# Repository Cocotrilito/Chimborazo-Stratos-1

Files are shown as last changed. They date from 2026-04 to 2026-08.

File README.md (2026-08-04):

# Chimborazo-Stratos-1 V2
"Designed at the world's closest point to the stars." - me =p A custom Model Rocket Flight Computer (CFC) designed for high-altitude stabilization and recovery. It features an IMU for orientation tracking and a barometer for apogee detection. The goal is to create a reliable, low-cost brain for amateur rocketry in Ecuador.
## The reason behind this project
**"When something is important enough, you do it even if the odds are not in your favor."** *— Elon Musk*
This project is born with the intent of giving my homecountry a posibility or even a first step to develop new technology, maybe *inspire* others just like Astrounauts or cientifics inspired me.
## It's Alive!

<p align="center">
  Chimborazo Stratos-1 running
</p>

<p align="center">
  
</p>

First bring-up worked. The IMU and the barometer both came up on I2C at `0x68` and `0x77`, and the board is now streaming live telemetry over serial at 115200 baud.

Ground pressure read **75207 Pa**. Sea level is 101325 Pa, so the board is literally measuring the real atmosphere of Quito at ~2800m. Altitude noise is around ±0.1m, which is good enough for apogee detection.

The flight state machine goes `ARMED → BOOST → COAST → APOGEE → DESCENT`. Liftoff fires on an acceleration spike above 25 m/s², apogee on a 2m drop from peak altitude. Sensors are read at 50Hz and the dashboard prints every 3 seconds.
## Schematic Overview

<p align="center">
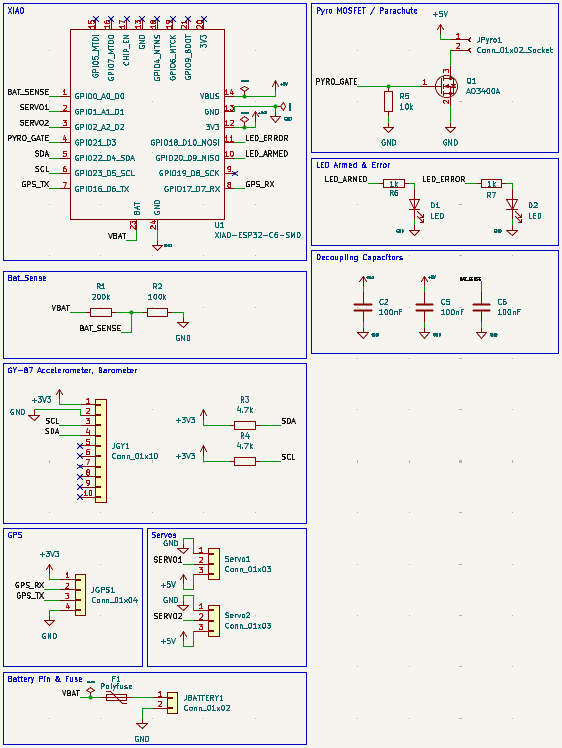
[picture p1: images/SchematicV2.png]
Chimborazo Stratos-1 Schematic model in KiCad
  
</p>

## PCB

<p align="center">
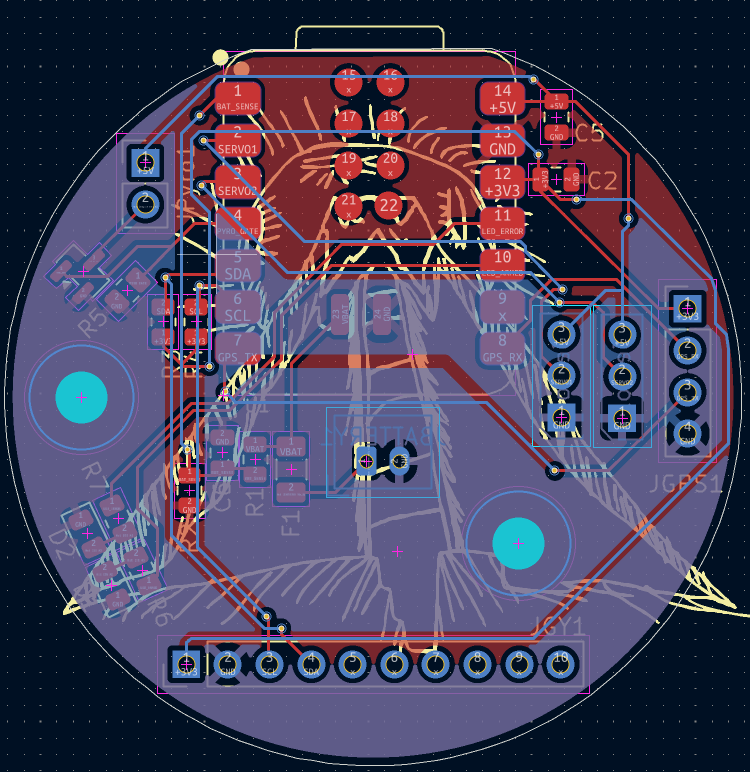
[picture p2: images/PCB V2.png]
PCB layout
  
</p>

<table>
  <tr>
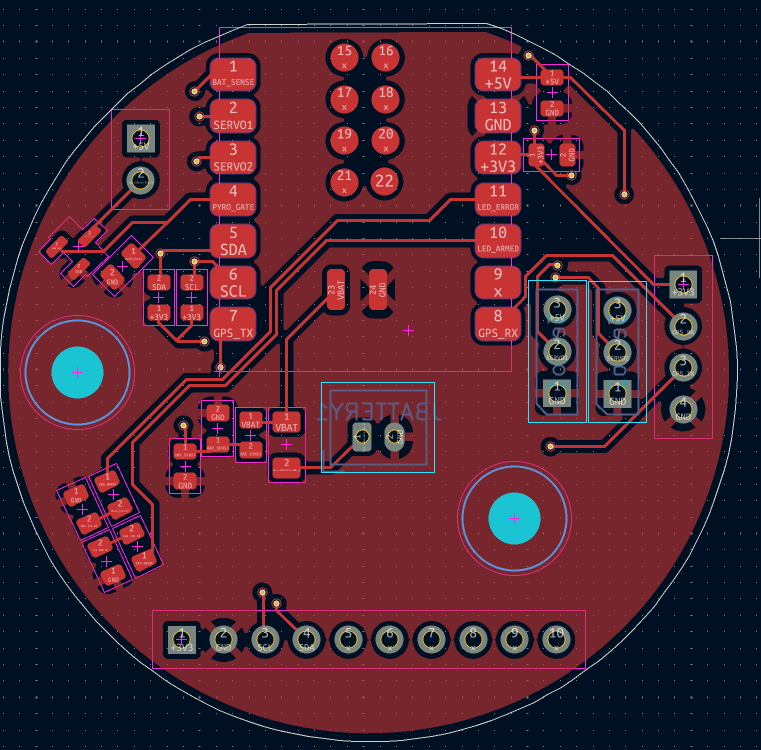
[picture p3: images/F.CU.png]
Front copper
    <td width="50%"></td>
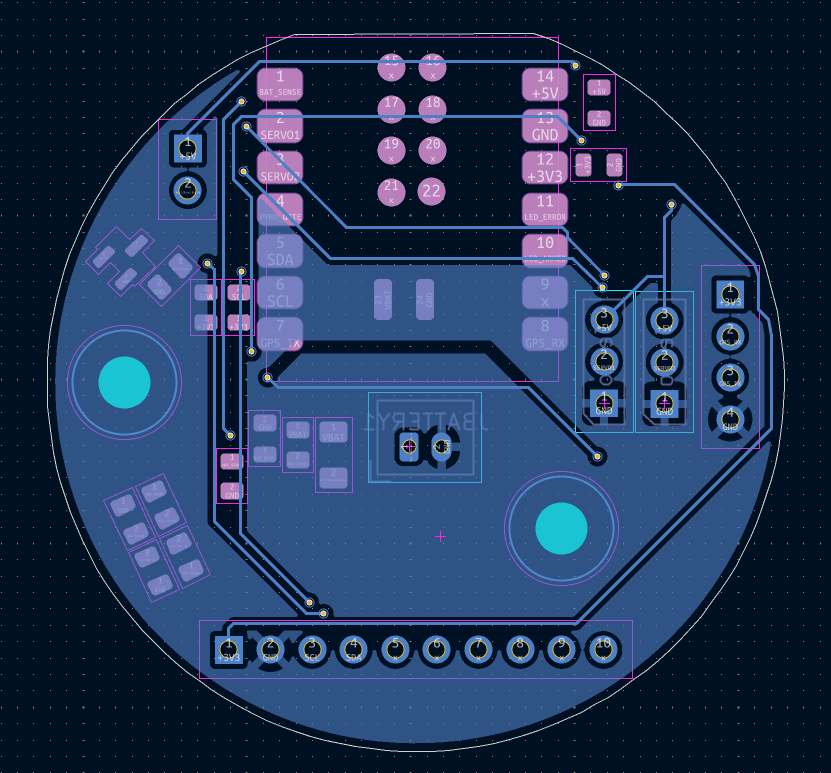
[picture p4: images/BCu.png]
Back copper
    <td width="50%"></td>
  </tr>
  <tr>
    <td align="center"><b>Front Copper</b></td>
    <td align="center"><b>Back Copper</b></td>
  </tr>
</table>

## CAD MODEL

<p align="center">
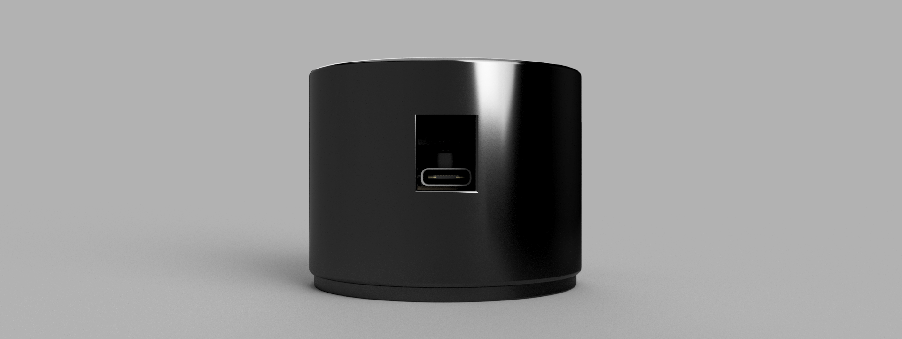
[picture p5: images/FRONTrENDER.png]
Final render
  
</p>

<table>
  <tr>
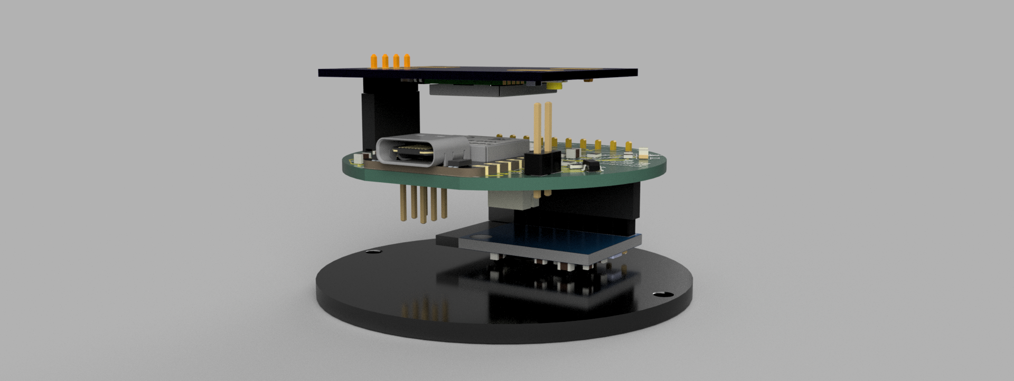
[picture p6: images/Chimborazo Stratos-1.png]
Side view
    <td width="50%"></td>
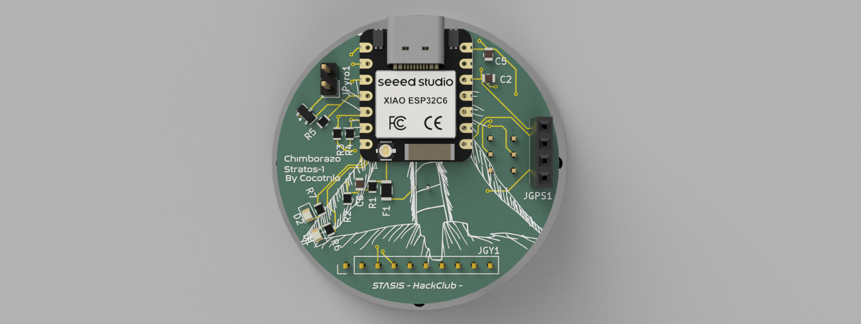
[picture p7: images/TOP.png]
Top view
    <td width="50%"></td>
  </tr>
  <tr>
    <td align="center"><b>Side View</b></td>
    <td align="center"><b>Top View</b></td>
  </tr>
</table>

## Bom 
| Name | Purpose | Qty | Total Cost (USD) | Link |
| :--- | :--- | :---: | :---: | :--- |
| **XIAO ESP32-C6** | Main Flight Computer / MCU | 1 | $11.08 | [AliExpress](https://www.aliexpress.com/item/3256808627180483.html) |
| **GY-87 10DOF** | IMU & Barometer (Orientation/Altitude) | 1 | $1.53 | [AliExpress](https://www.aliexpress.com/item/3256807064707842.html) |
| **ATGM336H GPS** | Global Positioning System Module | 1 | $1.93 | [AliExpress](https://www.aliexpress.com/item/3256810342214632.html) |
| **SG90 Servos (2pcs)** | Canard Actuators (Active Stabilization) | 1 | $1.33 | [AliExpress](https://www.aliexpress.com/item/3256807031850814.html) |
| **JST PH 2.0 Connectors** | LiPo Battery Connection Set | 1 | $1.53 | [AliExpress](https://www.aliexpress.com/item/3256808243626691.html) |
| **40-Pin Headers (M/F)** | Interconnection & Sensor Mounting | 1 | $0.93 | [AliExpress](https://www.aliexpress.com/item/3256811594914967.html) |
| **JLCPCB PCBA** | PCB Manufacturing + SMT Assembly | 1 | $22.46 | [JLCPCB](https://jlcpcb.com) |
## Things I learned the hard way
- The GY-87 has 8 pins starting with `VCC_IN` but my PCB only breaks out 4. Turns out you can feed 3.3V straight into the `3V3` pin and skip the module's onboard regulator entirely. Left `VCC_IN` hanging off the edge and it worked.
- The SG90 servos were browning out my USB port on startup and killing my uploads. In flight they go on the LiPo, never on USB.
- This GY-87 ships with a **BMP180**, not a BMP280. Needs the `Adafruit_BMP085` library.
- The HMC5883L magnetometer hides behind the MPU6050's auxiliary bus. It only shows up at `0x1E` after enabling bypass mode with `INT_PIN_CFG = 0x02`.
## What's next
- [ ] Solder the JST PH 2.0 for the LiPo
- [ ] GPS satellite lock (UART is open, needs open sky)
- [ ] Servo control and canard stabilization
- [ ] Onboard flight data logging
## Final Notes
Thanks for reading! made possible with http://stasis.hackclub.com/
New version! after review
## Dreams
*By cocotrilo*
**made with luv <3**

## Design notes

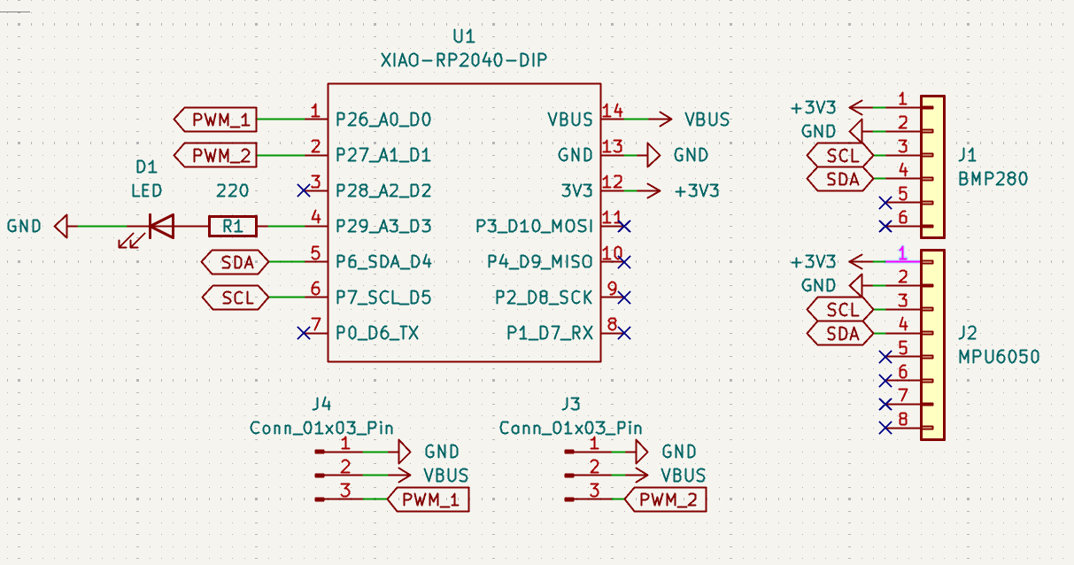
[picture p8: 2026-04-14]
images/Schematic.png

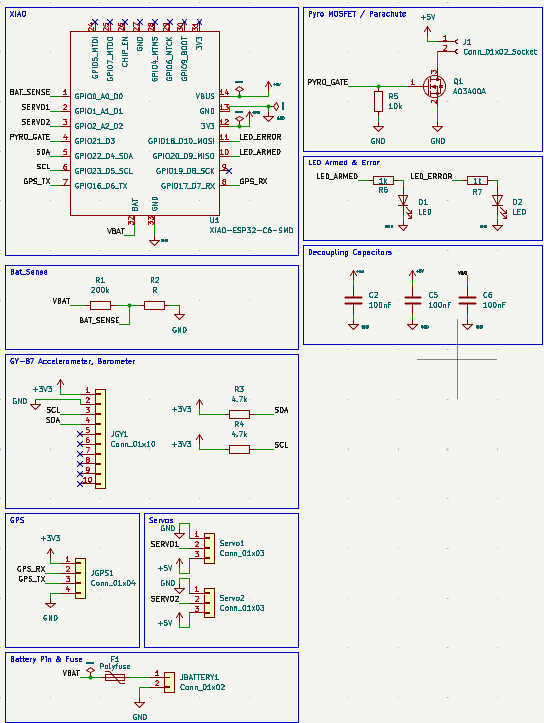
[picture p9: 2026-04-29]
images/SchematicUPDATE.png

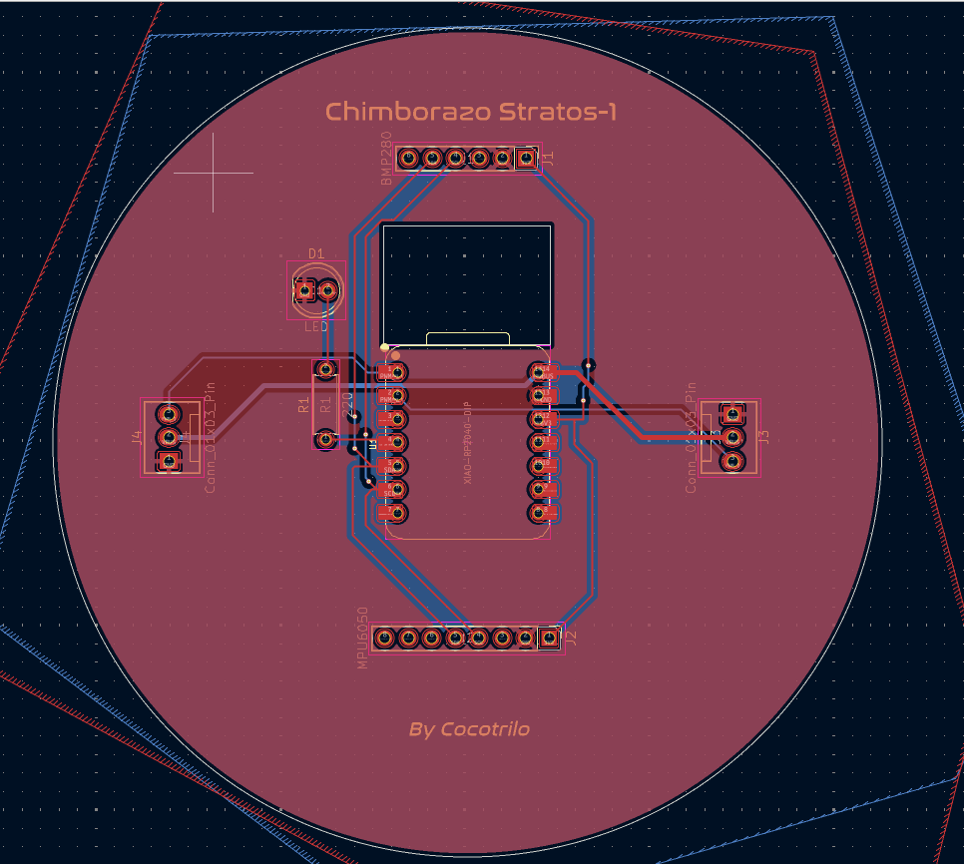
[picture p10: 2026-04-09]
images/08-04-26 PCB.png

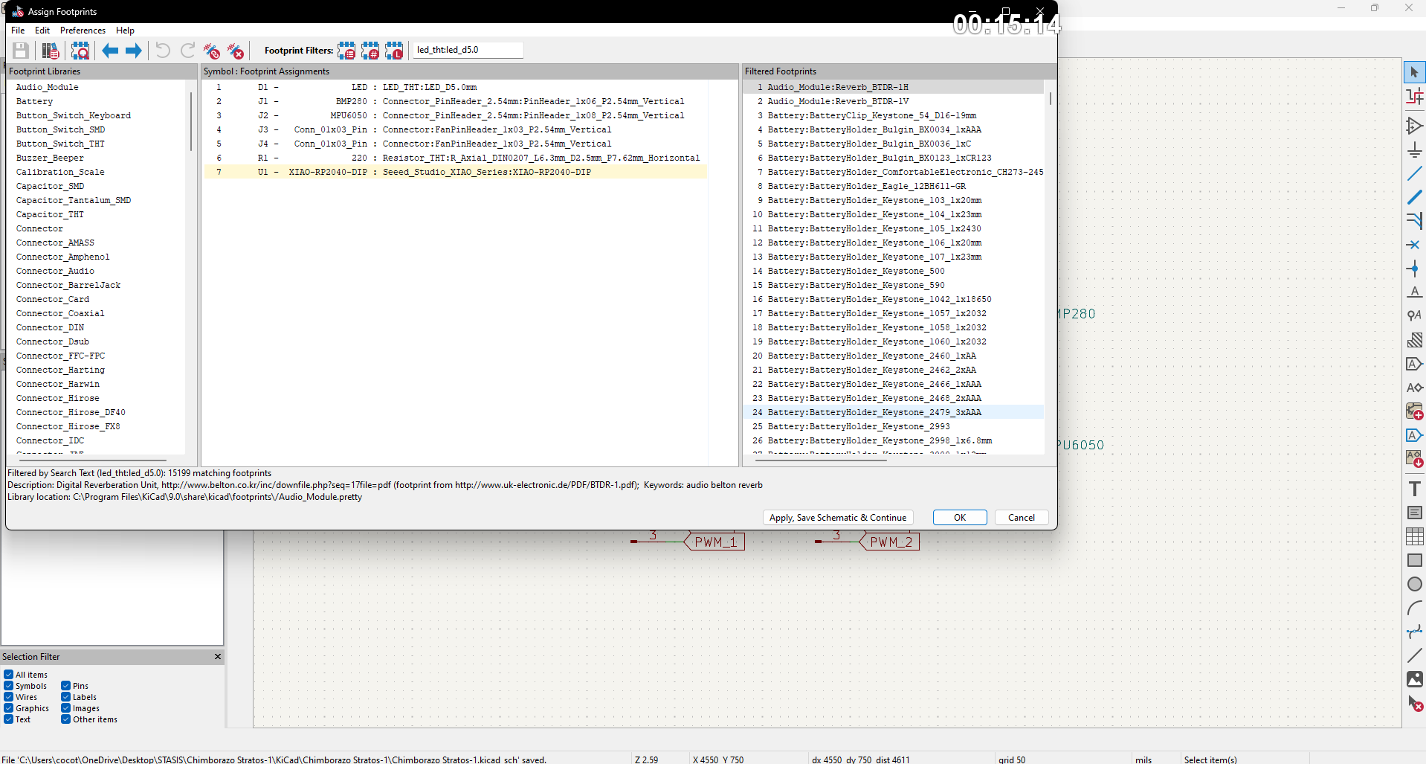
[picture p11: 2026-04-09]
images/08-04-26 FOOTPRITNS.png

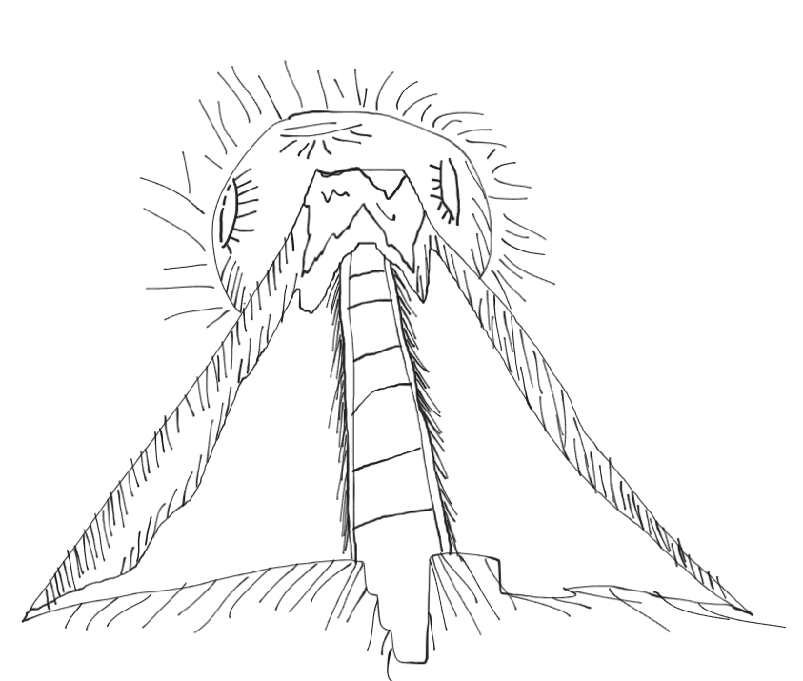
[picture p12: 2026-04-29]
images/art.png

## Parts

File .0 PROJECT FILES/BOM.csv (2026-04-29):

Name | Purpose | Qty | Total Cost (USD) | Link
XIAO ESP32-C6 | Main Flight Computer / MCU | 1 | 11.08 | https://www.aliexpress.com/item/3256808627180483.html
GY-87 10DOF | IMU & Barometer (Orientation/Altitude) | 1 | 1.53 | https://www.aliexpress.com/item/3256807064707842.html
ATGM336H GPS | Global Positioning System Module | 1 | 1.93 | https://www.aliexpress.com/item/3256810342214632.html
SG90 Servos (2pcs) | Canard Actuators (Active Stabilization) | 1 | 1.33 | https://www.aliexpress.com/item/3256807031850814.html
JST PH 2.0 Connectors | LiPo Battery Connection Set | 1 | 1.53 | https://www.aliexpress.com/item/3256808243626691.html
40-Pin Headers (M/F) | Interconnection & Sensor Mounting | 1 | 0.93 | https://www.aliexpress.com/item/3256811594914967.html
JLCPCB PCBA | PCB Manufacturing + SMT Assembly | 1 | 22.46 | https://jlcpcb.com
Taxes & Customs | Estimated Import Duties | 1 | 5 | -

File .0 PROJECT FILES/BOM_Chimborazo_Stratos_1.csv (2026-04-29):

Item | Descripcion | Proveedor | Cantidad | Precio_USD | Enlace | Subtotal
XIAO ESP32-C6 | Microcontrolador Principal | AliExpress | 1 | 11.08 | https://www.aliexpress.com/item/3256808627180483.html | 11.08
GY-87 10DOF | Sensor IMU + Barómetro | AliExpress | 1 | 1.53 | https://www.aliexpress.com/item/3256807064707842.html | 1.53
GPS ATGM336H | Posicionamiento Global | AliExpress | 1 | 1.93 | https://www.aliexpress.com/item/3256810342214632.html | 1.93
Servos SG90 (2pcs) | Actuadores Canards | AliExpress | 1 | 1.33 | https://www.aliexpress.com/item/3256807031850814.html | 1.33
JST PH 2.0 Connector | Conector Batería | AliExpress | 1 | 1.53 | https://www.aliexpress.com/item/3256808243626691.html | 1.53
40 Pin Headers (M/F) | Conectores | AliExpress | 1 | 0.93 | https://www.aliexpress.com/item/3256811594914967.html | 0.93
JLCPCB PCBA | PCB + Montaje SMD | JLCPCB | 1 | 22.46 | https://jlcpcb.com | 22.46
Tax / Impuestos | Aranceles estimados | Aduana | 1 | 5.0 | - | 5.0

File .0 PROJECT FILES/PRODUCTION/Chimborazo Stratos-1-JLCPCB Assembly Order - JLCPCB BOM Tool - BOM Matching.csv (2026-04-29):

JLCPCB BOM Tool - BOM Matching
BOM name：Chimborazo Stratos-1-JLCPCB Assembly Order.xlsx |  |  | Download Time：2026-04-30 01:16:50 |  |  |  | * Our matching results are updated in real-time, but stock and prices may change. If it's been over 24 hours, please re-match before placing your order.
PCB Assembled Qty：5 |  |  | Est. Total Price：0.4023
Your BOM |  |  |  |  | Matched Parts |  |  |  |  |  |  | Order Information
Top Designator | Bottom Designator | Comment | Footprint | JLCPCB Part # | Matches | Part # | Manufacturer | Footprint | Description | Category | Warning | JLCPCB Part # | Product link | Lib Type | Qty | Source | Total Price ($)
C2,C5,C6 |  | 100nF | C_0805_2012Metric |  | Select by Customer | CC0805KRX7R9BB104 | YAGEO | 0805 | 100nF 50V X7R ±10% 0805 Multilayer Ceramic Capacitors MLCC - SMD/SMT ROHS | Multilayer Ceramic Capacitors MLCC - SMD/SMT |  | C49678 | https://jlcpcb.com/partdetail/YAGEO-CC0805KRX7R9BB104/C49678 | Basic | 6 | 6 JLCPCB | 0.0312
D1,D2 |  | LED | LED_0805_2012Metric |  | Select by Customer | KT-0805Y | Hubei KENTO Elec | 0805 | -40℃~+85℃ 1.8V~2.4V 120° 175mcd 40mW 584nm~594nm 596nm Discrete Diode Water Clear Yellow 0805 LED Indication - Discrete ROHS | LED Indication - Discrete | 1.The comment (KT-0805Y) of this part does not match the one (LED) provided in your BOM. Please confirm; | C2296 | https://jlcpcb.com/partdetail/Hubei_KENTOElec-KT0805Y/C2296 | Basic | 4 | 4 JLCPCB | 0.06
F1 |  | Polyfuse | Fuse_1206_3216Metric |  | Select by Customer | 1206W4F6800T5E | UNI-ROYAL(Uniroyal Elec) | 1206 | -55℃~+155℃ 200V 250mW 680Ω Thick Film Resistor ±1% ±100ppm/℃ 1206 Chip Resistor - Surface Mount ROHS | Chip Resistor - Surface Mount |  | C17975 | https://jlcpcb.com/partdetail/18663-1206W4F6800T5E/C17975 | Extended | 15 | 15 JLCPCB | 0.0555
Q1 |  | AO3400A | SOT-23 |  | Select by Customer | AO3400A | Alpha & Omega Semicon | SOT-23 | -55℃~+150℃ 1 N-channel 1.45V 1.4W 30V 48mΩ@2.5V 5.7A 50pF 630pF 75pF 7nC@10V N-Channel SOT-23 MOSFETs ROHS | MOSFETs |  | C20917 | https://jlcpcb.com/partdetail/Alpha_OmegaSemicon-AO3400A/C20917 | Basic | 2 | 2 JLCPCB | 0.1634
R1 |  | 200k | R_0805_2012Metric |  | Select by Customer | 0805W8F2003T5E | UNI-ROYAL(Uniroyal Elec) | 0805 | -55℃~+155℃ 125mW 150V 200kΩ Thick Film Resistor ±1% ±100ppm/℃ 0805 Chip Resistor - Surface Mount ROHS | Chip Resistor - Surface Mount | 1.The comment (0805W8F2003T5E) of this part does not match the one (200k) provided in your BOM. Please confirm; | C17539 | https://jlcpcb.com/partdetail/18227-0805W8F2003T5E/C17539 | Basic | 2 | 2 JLCPCB | 0.0056
R2 |  | 100k | R_0805_2012Metric |  | Select by Customer | RC0805FR-07100KL | YAGEO | 0805 | -55℃~+155℃ 100kΩ 125mW 150V Thick Film Resistor ±1% ±100ppm/℃ 0805 Chip Resistor - Surface Mount ROHS | Chip Resistor - Surface Mount | 1.The comment (RC0805FR-07100KL) of this part does not match the one (100k) provided in your BOM. Please confirm; | C96346 | https://jlcpcb.com/partdetail/YAGEO-RC0805FR07100KL/C96346 | Extended | 20 | 20 JLCPCB | 0.06
R3,R4 |  | 4.7k | R_0805_2012Metric |  | Select by Customer | 0805W8F4701T5E | UNI-ROYAL(Uniroyal Elec) | 0805 | -55℃~+155℃ 125mW 150V 4.7kΩ Thick Film Resistor ±1% ±100ppm/℃ 0805 Chip Resistor - Surface Mount ROHS | Chip Resistor - Surface Mount | 1.The comment (0805W8F4701T5E) of this part does not match the one (4.7k) provided in your BOM. Please confirm; | C17673 | https://jlcpcb.com/partdetail/18361-0805W8F4701T5E/C17673 | Basic | 4 | 4 JLCPCB | 0.0088
R5 |  | 10k | R_0805_2012Metric |  | Select by Customer | 0805W8F1002T5E | UNI-ROYAL(Uniroyal Elec) | 0805 | -55℃~+155℃ 10kΩ 125mW 150V Thick Film Resistor ±1% ±100ppm/℃ 0805 Chip Resistor - Surface Mount ROHS | Chip Resistor - Surface Mount | 1.The comment (0805W8F1002T5E) of this part does not match the one (10k) provided in your BOM. Please confirm; | C17414 | https://jlcpcb.com/partdetail/18102-0805W8F1002T5E/C17414 | Basic | 2 | 2 JLCPCB | 0.0058
R6,R7 |  | 1k | R_0805_2012Metric |  | Select by Customer | 0805W8F1001T5E | UNI-ROYAL(Uniroyal Elec) | 0805 | -55℃~+155℃ 125mW 150V 1kΩ Thick Film Resistor ±1% ±100ppm/℃ 0805 Chip Resistor - Surface Mount ROHS | Chip Resistor - Surface Mount | 1.The comment (0805W8F1001T5E) of this part does not match the one (1k) provided in your BOM. Please confirm; | C17513 | https://jlcpcb.com/partdetail/18201-0805W8F1001T5E/C17513 | Basic | 4 | 4 JLCPCB | 0.012

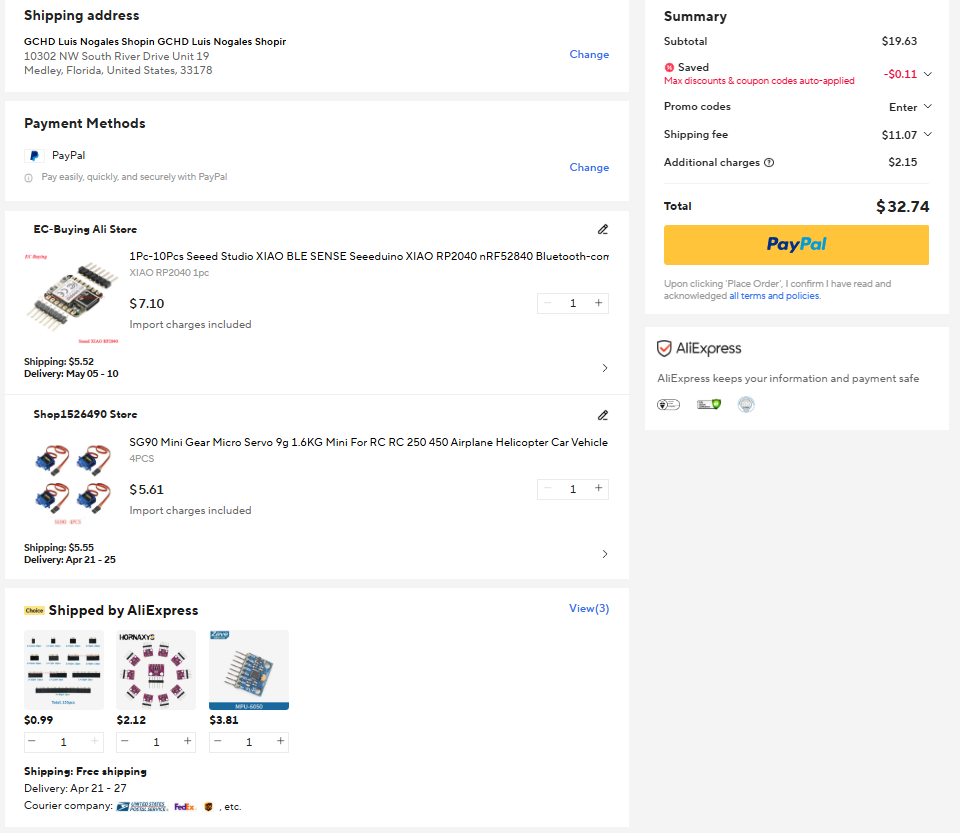
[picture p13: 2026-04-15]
images/cart BOM aliexpress.png

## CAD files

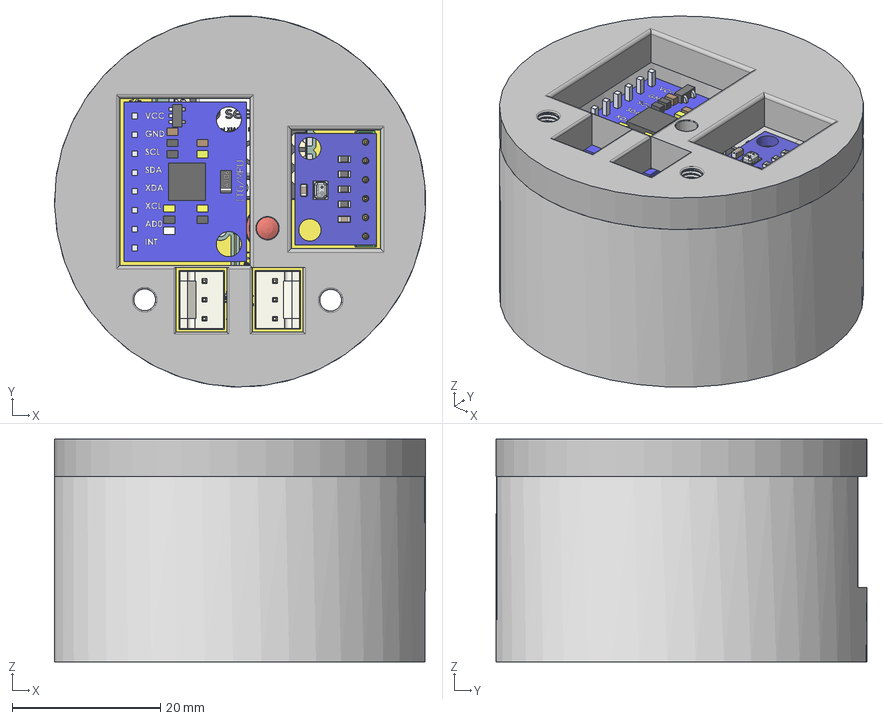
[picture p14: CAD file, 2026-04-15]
CAD/0. STEP FILES/Chimborazo Stratos-1.step
50.0 x 50.0 x 30.0 mm

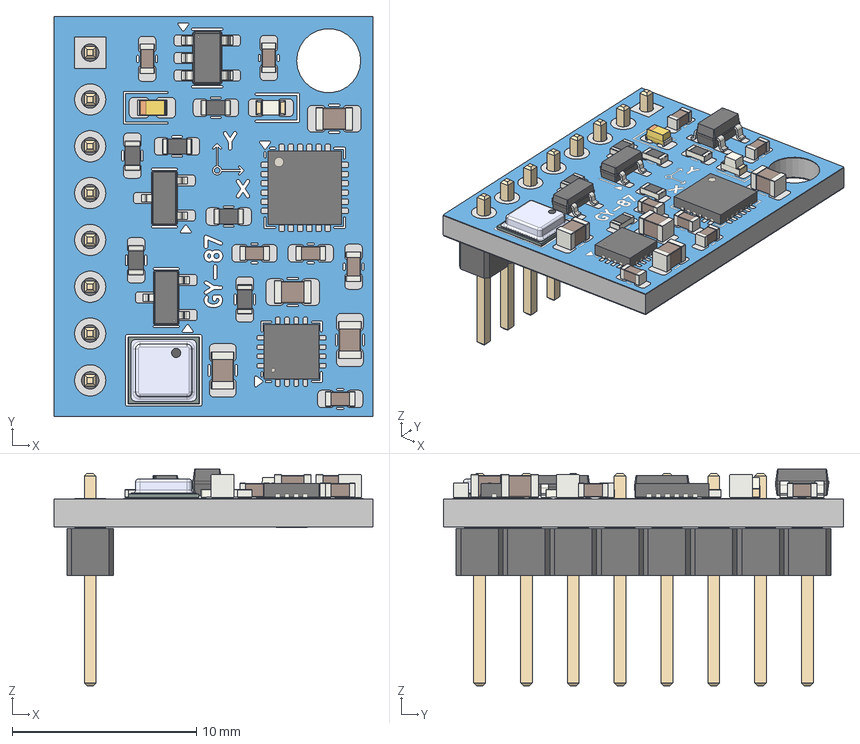
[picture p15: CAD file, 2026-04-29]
CAD/Assets V2/gy-87-10dof-imu-1.snapshot.2/GY87_10DOF_IMU.step
17.3 x 21.7 x 11.8 mm
C_0603_1608Metric x 6
QFN-24-1EP_4x4mm_P0.5mm_EP2.7x2.7mm
SOT-23-5
SOT-23 x 2
LED_0603_1608Metric
BMP180
QFN-16-1EP_3x3mm_P0.5mm_EP1.7x1.7mm
CP_EIA-1608-10_AVX-L
R_0603_1608Metric x 6
C_0805_2012Metric x 4
PinHeader_1x08_P2.54mm_Vertical
GY87_10DOF_IMU_pad
GY87_10DOF_IMU_silkscreen
GY87_10DOF_IMU_soldermask
GY87_10DOF_IMU_PCB

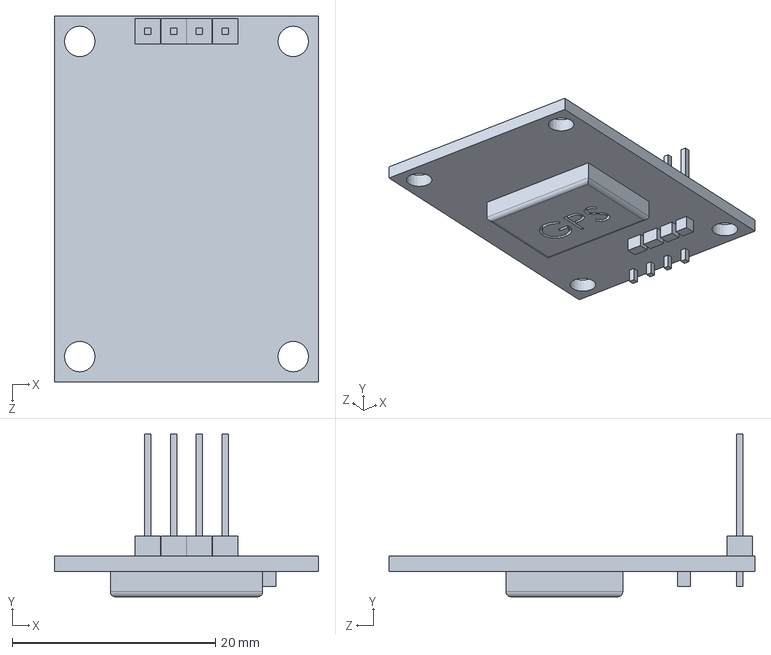
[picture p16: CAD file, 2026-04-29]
CAD/Assets V2/neo-6m-gps-module-1.snapshot.2/neo6mGps.SLDPRT
26.0 x 16.0 x 36.0 mm

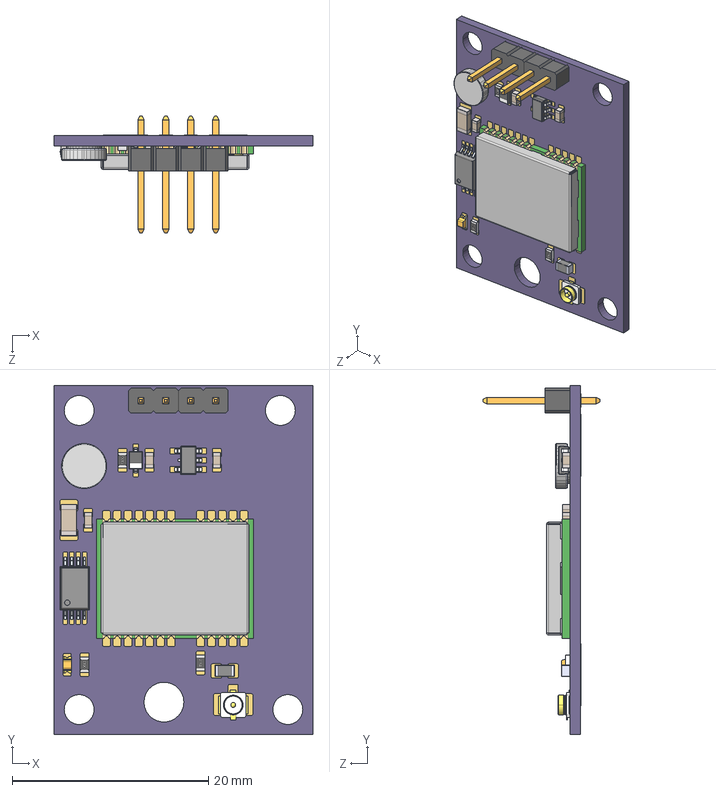
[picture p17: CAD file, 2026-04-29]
CAD/Assets V2/neo-6m-module-1.snapshot.2/NEO-6M.STEP
26.3 x 35.6 x 11.9 mm
NEO-6M_v100
NEO-6M_v100-bottom
NEO-6M_v100-top

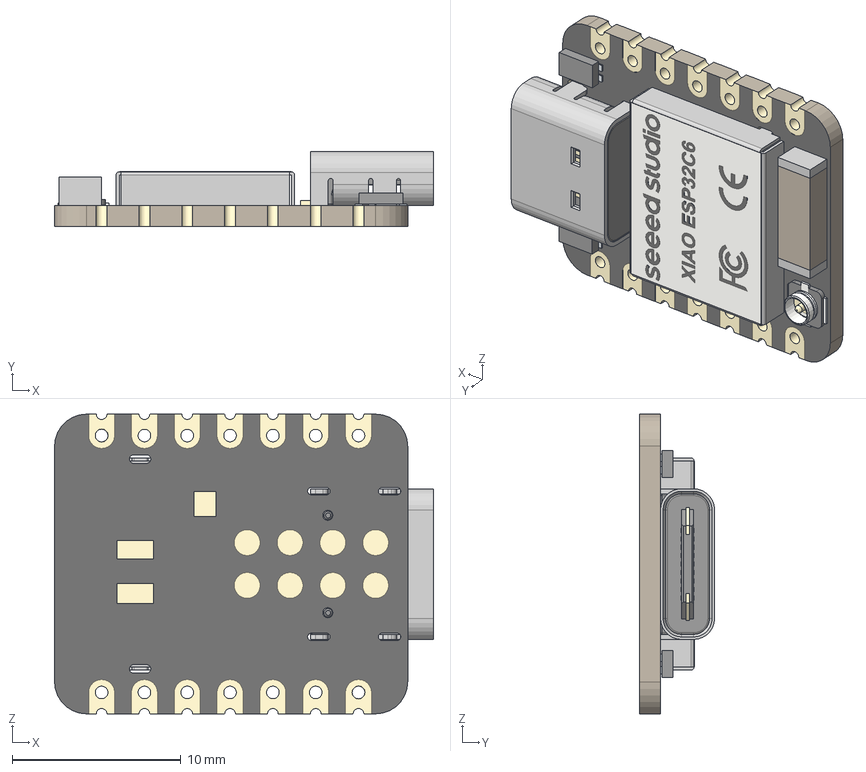
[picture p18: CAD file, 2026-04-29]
CAD/Assets V2/seeed-studio-xiao-esp32c6-1.snapshot.2/Seeed Studio XIAO ESP32C6 v2.step
22.5 x 4.46 x 17.8 mm
BOSS-EXTRUDE14_8_
BOSS-EXTRUDE7_4_
BOSS-EXTRUDE7_3_
BOSS-EXTRUDE14_4_
BOSS-EXTRUDE14_2_
BOSS-EXTRUDE14_11_
BOSS-EXTRUDE7_7_
BOSS-EXTRUDE14_9_
BOSS-EXTRUDE14_3_
BOSS-EXTRUDE14_7_
MIRROR2
BOSS-EXTRUDE14_5_
BOSS-EXTRUDE14_12_
BOSS-EXTRUDE7_8_
BOSS-EXTRUDE7_1_
BOSS-EXTRUDE14_10_
BOSS-EXTRUDE7_9_
BOSS-EXTRUDE14_6_
BOSS-EXTRUDE14_1_
BOSS-EXTRUDE7_6_
BOSS-EXTRUDE7_2_
CUT-EXTRUDE5
BOSS-EXTRUDE7_5_
Shield
Pins x 2
U.FL-R-SMT-1_10_ v1

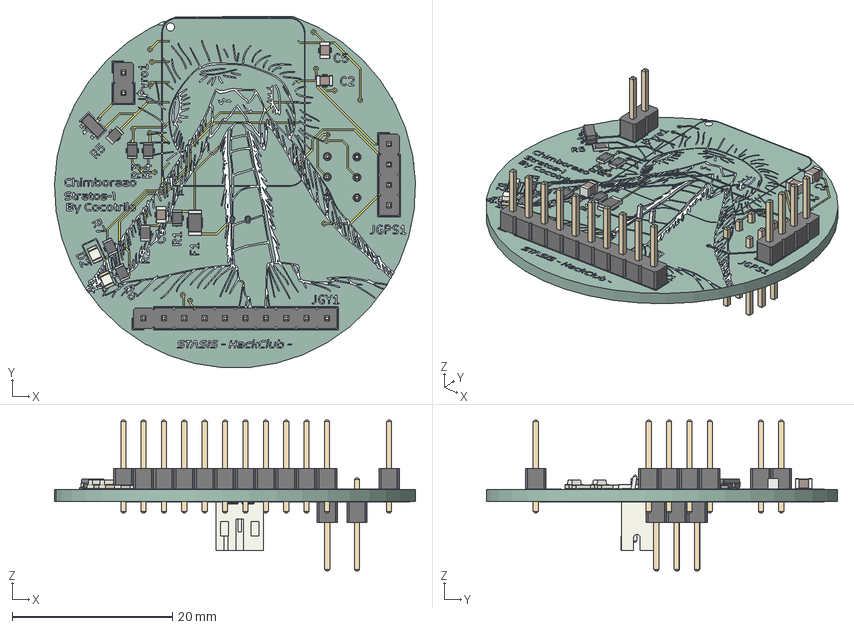
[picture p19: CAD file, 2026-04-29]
CAD/REVIEW V2/CS1.step
45.0 x 43.8 x 18.8 mm
C_0805_2012Metric x 3
PinHeader_1x02_P2.54mm_Vertical
R_0805_2012Metric x 7
LED_0805_2012Metric x 2
SOT-23
PinHeader_1x04_P2.54mm_Vertical
PinHeader_1x10_P2.54mm_Vertical
Fuse_1206_3216Metric
JST_PH_B2B-PH-K_1x02_P2.00mm_Vertical
PinHeader_1x03_P2.54mm_Vertical x 2
Chimborazo Stratos-1_copper
Chimborazo Stratos-1_via
Chimborazo Stratos-1_silkscreen x 2
Chimborazo Stratos-1_PCB

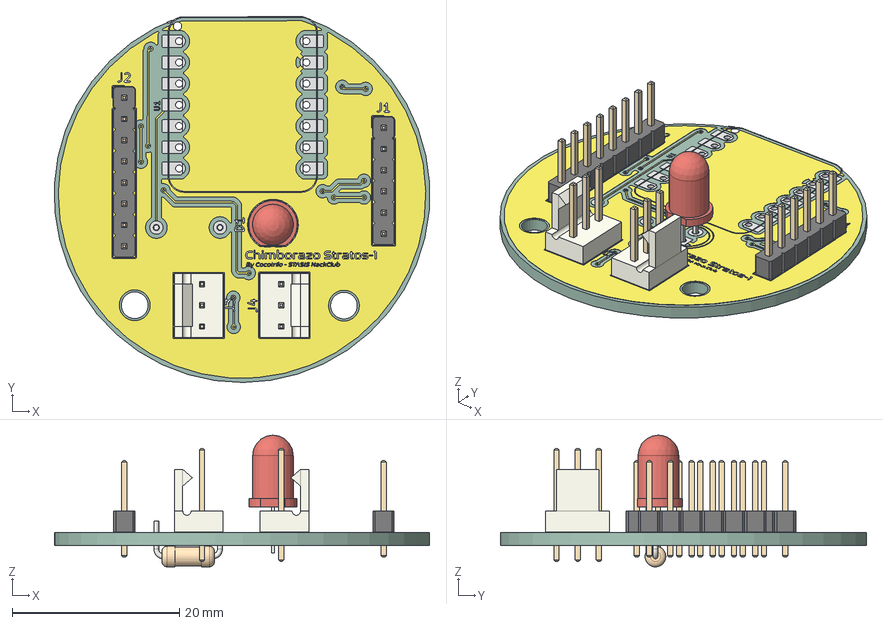
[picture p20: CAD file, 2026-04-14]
KiCad/Chimborazo Stratos-1/Chimborazo Stratos-1.step
44.9 x 43.8 x 15.8 mm
LED_D5.0mm
PinHeader_1x06_P2.54mm_Vertical
FanPinHeader_1x03_P2.54mm_Vertical x 2
PinHeader_1x08_P2.54mm_Vertical
R_Axial_DIN0207_L6.3mm_D2.5mm_P7.62mm_Horizontal
Chimborazo Stratos-1_copper
Chimborazo Stratos-1_pad
Chimborazo Stratos-1_via
Chimborazo Stratos-1_silkscreen x 2
Chimborazo Stratos-1_PCB

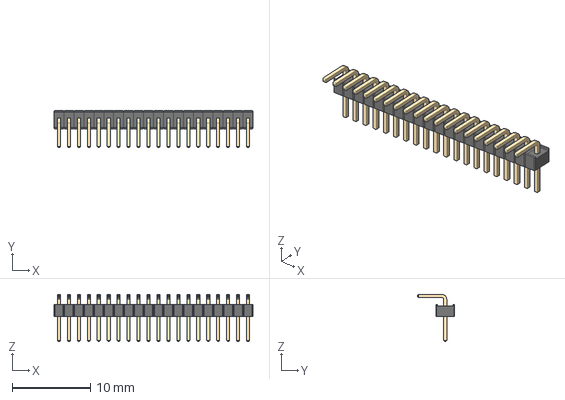
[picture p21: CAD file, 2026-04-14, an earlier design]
CAD/assets/1-27mm-header-pin-right-angle-1.snapshot.1/1.27mm Right Angle Pinhead 20.step
25.4 x 4.75 x 6.00 mm

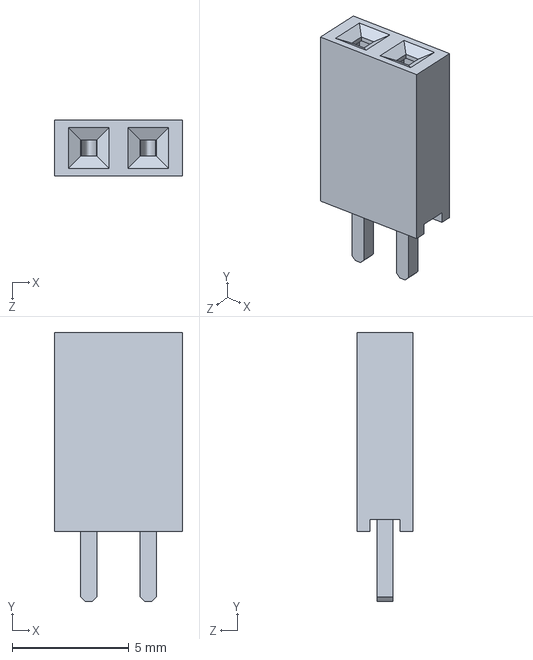
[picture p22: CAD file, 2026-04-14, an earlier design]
CAD/assets/2-54mm-female-pin-header-1.snapshot.3/100mil Female Pin Header.SLDPRT
5.48 x 11.5 x 2.40 mm

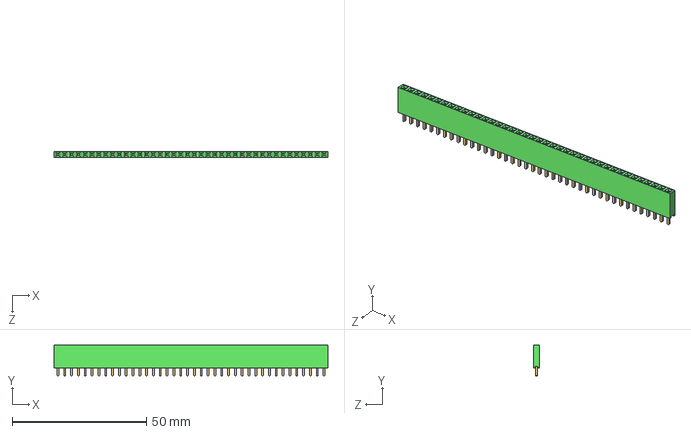
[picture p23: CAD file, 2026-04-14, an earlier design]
CAD/assets/2-54mm-female-pin-header-1.snapshot.3/steps/100mill Female Pin Header_40P_Gr.STEP
102.0 x 11.5 x 2.40 mm

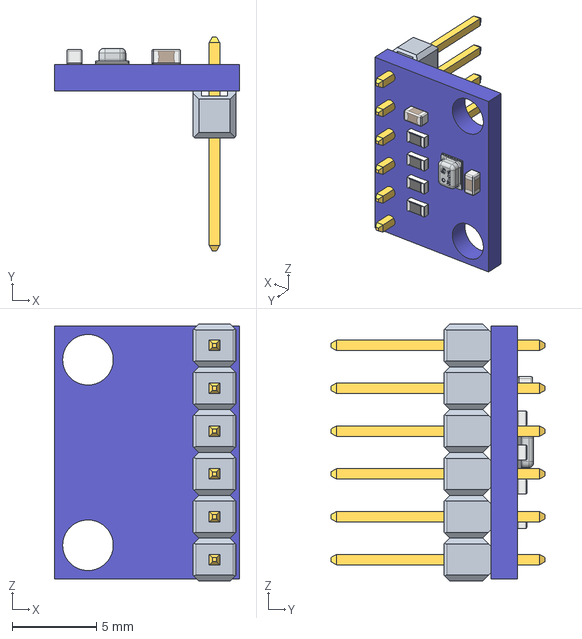
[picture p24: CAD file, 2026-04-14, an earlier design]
CAD/assets/bmp280-module-1.snapshot.1/bmp280_module.stp
11.0 x 12.7 x 15.2 mm

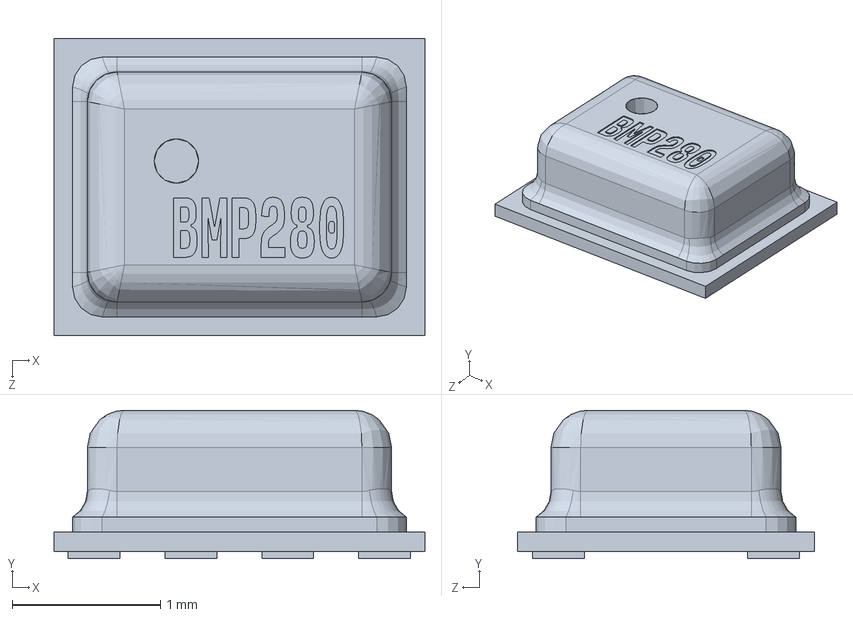
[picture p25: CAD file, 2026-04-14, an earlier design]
CAD/assets/bmp280/GY-91/Components/BMP280.SLDPRT
2.50 x 1.00 x 2.00 mm

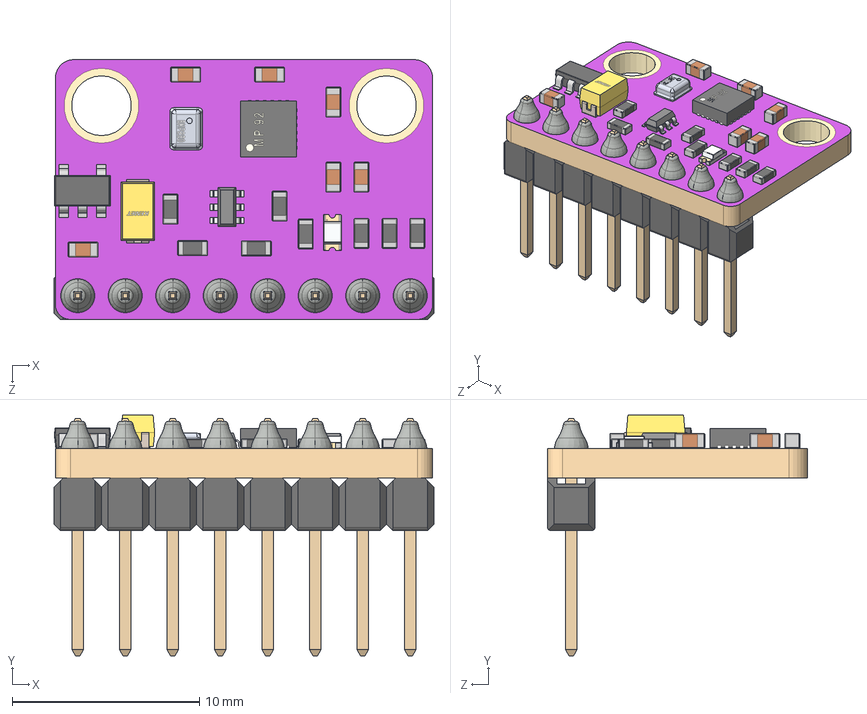
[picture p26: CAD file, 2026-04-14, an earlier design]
CAD/assets/bmp280/GY-91/GY-91_MPU9250+BMP280 - Pins Down.STEP
20.3 x 12.9 x 13.9 mm

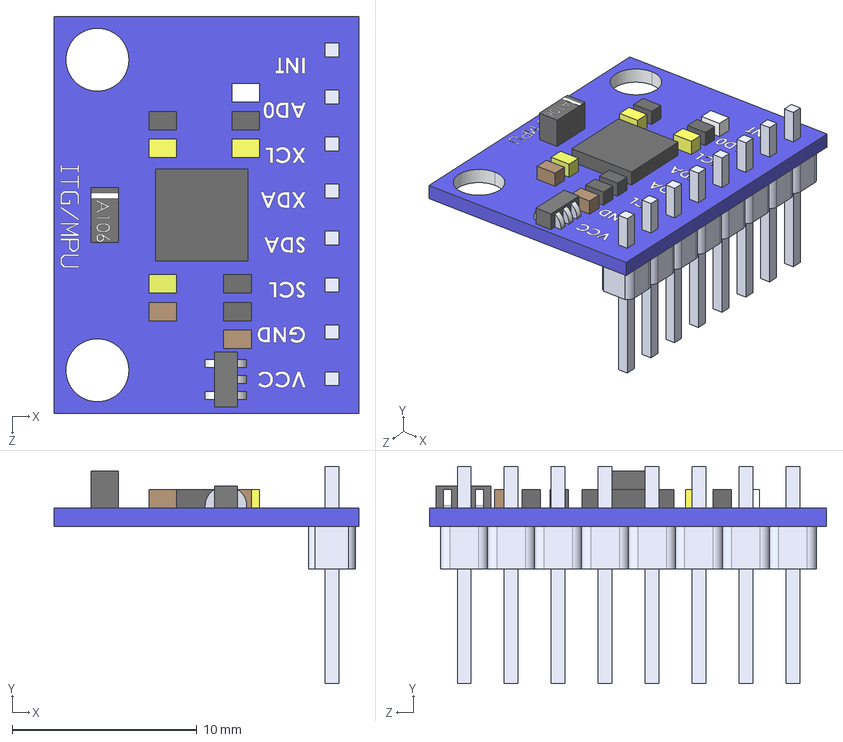
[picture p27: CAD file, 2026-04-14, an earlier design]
CAD/assets/itg-mpu-gy-521-1.snapshot.16/ITG-MPU.STEP
16.5 x 11.8 x 21.5 mm
8 Header-Pin
Placa_Base

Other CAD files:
CAD/assets/itg-mpu-gy-521-1.snapshot.16/Partes/Placa_Base.SLDPRT
CAD/assets/2-54mm-female-pin-header-1.snapshot.3/steps/100mill Female Pin Header_4P_Bk.STEP
CAD/assets/bmp280/GY-91/Components/solder.SLDPRT
CAD/assets/bmp280/GY-91/GY-91_MPU9250+BMP280 - Basic.STEP
.0 PROJECT FILES/CSTRATOS Fusion.f3d
CAD/0. STEP FILES/Chimborazo Stratos-1.f3d
CAD/Assets V2/neo-6m-module-1.snapshot.2/NEO-6M.x_t
CAD/assets/2-54mm-female-pin-header-1.snapshot.3/steps/100mil Female Pin Header_2P_Bk.STEP
CAD/assets/2-54mm-female-pin-header-1.snapshot.3/steps/100mill Female Pin Header_10P_Bk.STEP
CAD/assets/2-54mm-female-pin-header-1.snapshot.3/steps/100mill Female Pin Header_10P_Gr.STEP
CAD/assets/2-54mm-female-pin-header-1.snapshot.3/steps/100mill Female Pin Header_12P_Bk.STEP
CAD/assets/2-54mm-female-pin-header-1.snapshot.3/steps/100mill Female Pin Header_12P_Gr.STEP
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

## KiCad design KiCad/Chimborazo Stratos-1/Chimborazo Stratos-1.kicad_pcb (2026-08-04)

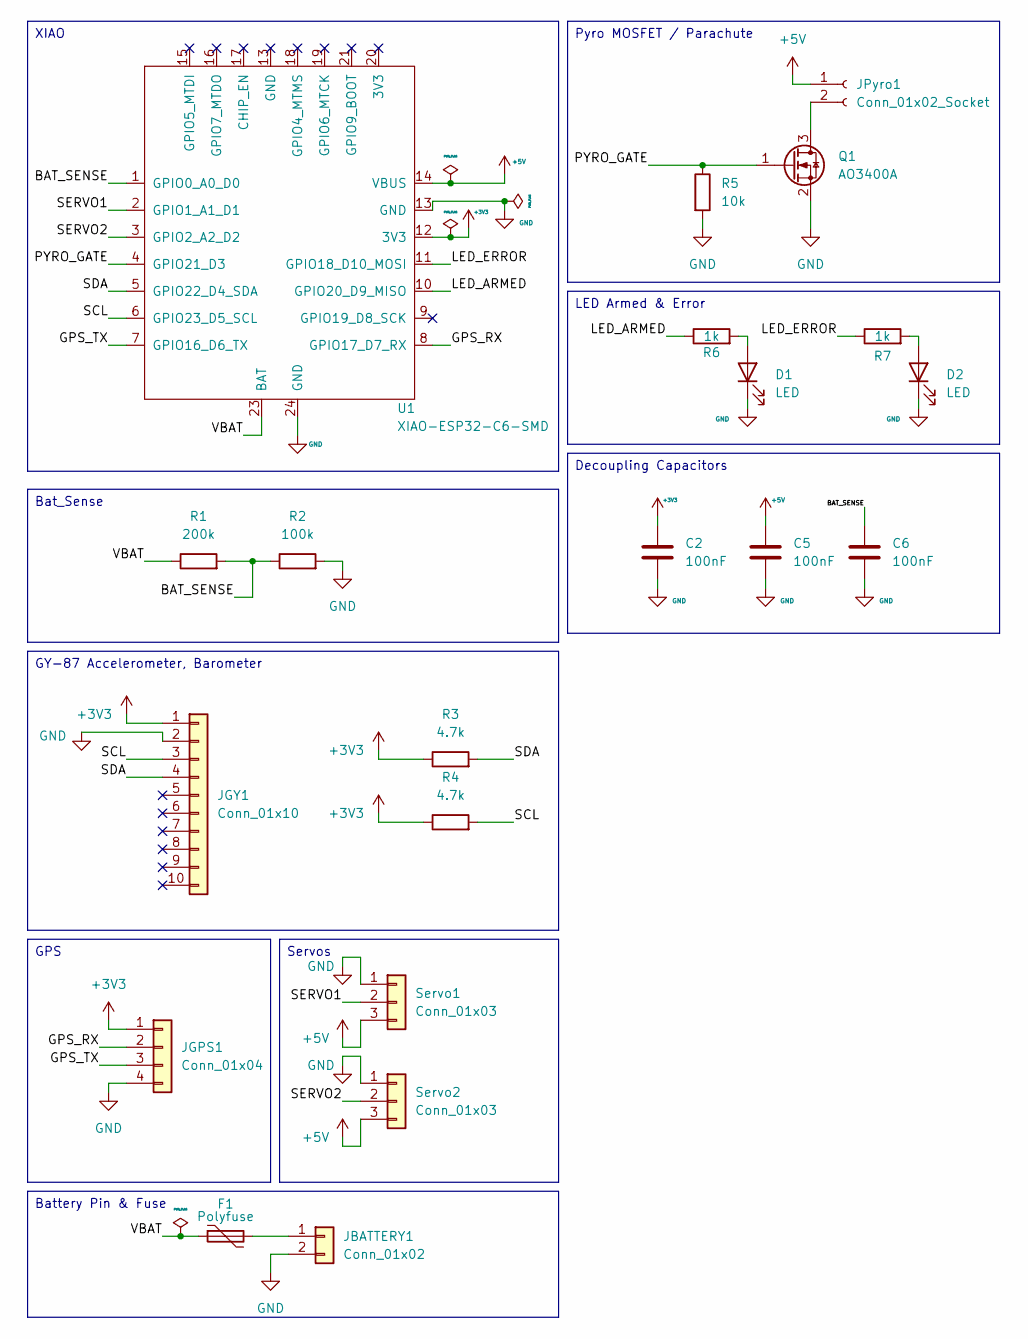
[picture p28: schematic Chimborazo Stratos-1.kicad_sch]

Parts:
C2, C5, C6: 100nF; C_0805_2012Metric
D1, D2: LED; LED_0805_2012Metric
F1: Polyfuse; Fuse_1206_3216Metric
JBATTERY1: Conn_01x02; JST_PH_B2B-PH-K_1x02_P2.00mm_Vertical
JGPS1: Conn_01x04; PinHeader_1x04_P2.54mm_Vertical
JGY1: Conn_01x10; PinHeader_1x10_P2.54mm_Vertical
JPyro1: Conn_01x02_Socket; PinHeader_1x02_P2.54mm_Vertical
Q1: AO3400A; SOT-23
R1: 200k; R_0805_2012Metric
R2: 100k; R_0805_2012Metric
R3, R4: 4.7k; R_0805_2012Metric
R5: 10k; R_0805_2012Metric
R6, R7: 1k; R_0805_2012Metric
Servo1, Servo2: Conn_01x03; PinHeader_1x03_P2.54mm_Vertical
U1: XIAO-ESP32-C6-SMD

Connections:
+3V3: C2.1, JGPS1.1, JGY1.1, R3.1, R4.1, U1.12 (3V3)
+5V: C5.1, JPyro1.1, Servo1.3, Servo2.3, U1.14 (VBUS)
/BAT_SENSE: C6.1, R1.2, R2.1, U1.1 (GPIO0_A0_D0)
/GPS_RX: JGPS1.2, U1.8 (GPIO17_D7_RX)
/GPS_TX: JGPS1.3, U1.7 (GPIO16_D6_TX)
/LED_ARMED: R6.1, U1.10 (GPIO20_D9_MISO)
/LED_ERROR: R7.1, U1.11 (GPIO18_D10_MOSI)
/PYRO_GATE: Q1.1 (G), R5.1, U1.4 (GPIO21_D3)
/SCL: JGY1.3, R4.2, U1.6 (GPIO23_D5_SCL)
/SDA: JGY1.4, R3.2, U1.5 (GPIO22_D4_SDA)
/SERVO1: Servo1.2, U1.2 (GPIO1_A1_D1)
/SERVO2: Servo2.2, U1.3 (GPIO2_A2_D2)
/VBAT: F1.1, R1.1, U1.23 (BAT)
GND: C2.2, C5.2, C6.2, D1.1 (K), D2.1 (K), JBATTERY1.2, JGPS1.4, JGY1.2, Q1.2 (S), R2.2, R5.2, Servo1.1, Servo2.1, U1.13 (GND), U1.24 (GND)
unnamed: D1.2 (A), R6.2
unnamed: D2.2 (A), R7.2
unnamed: F1.2, JBATTERY1.1
unnamed: JPyro1.2, Q1.3 (D)

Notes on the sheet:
Pyro MOSFET / Parachute
Servos
Bat_Sense
GY-87 Accelerometer, Barometer
Battery Pin & Fuse
XIAO
GPS
LED Armed & Error
Decoupling Capacitors

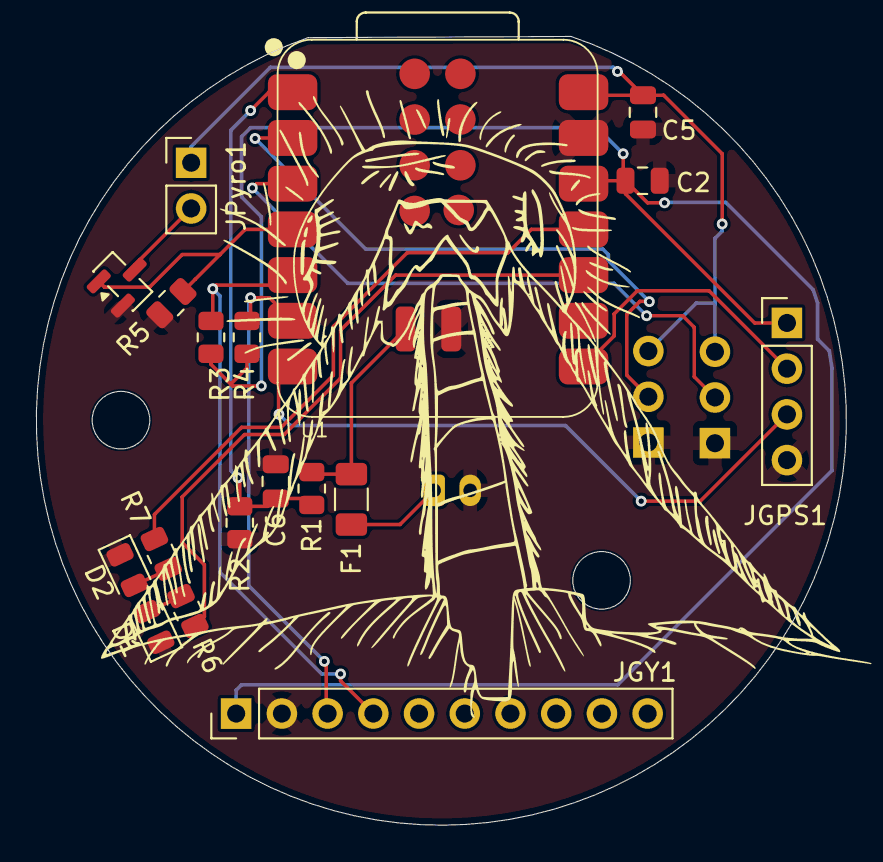
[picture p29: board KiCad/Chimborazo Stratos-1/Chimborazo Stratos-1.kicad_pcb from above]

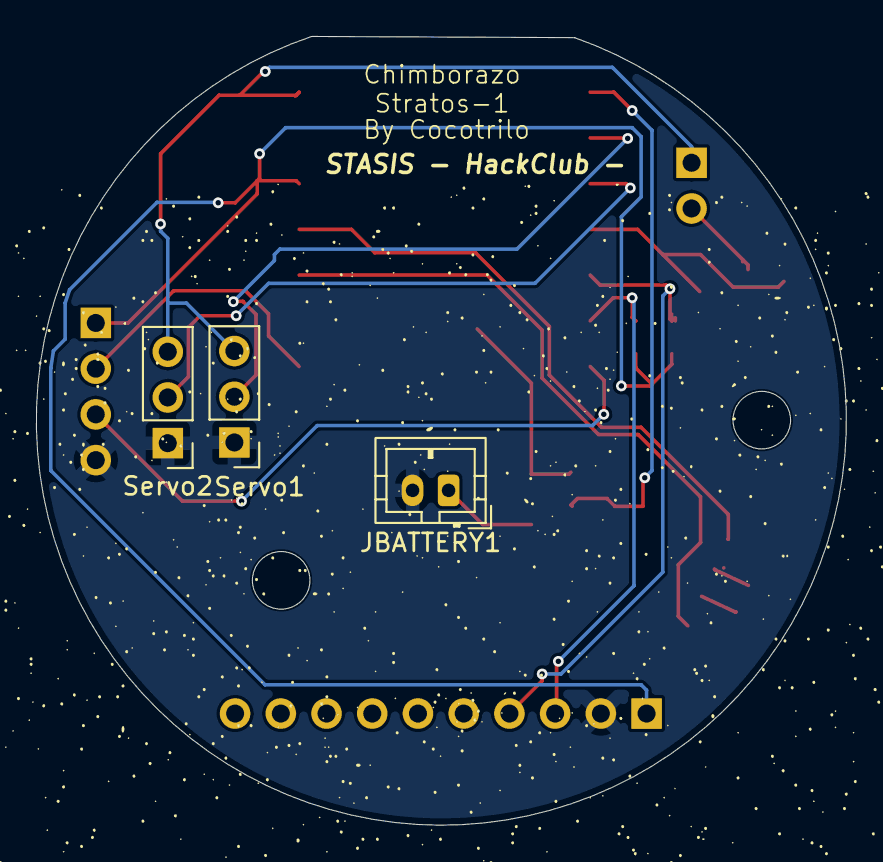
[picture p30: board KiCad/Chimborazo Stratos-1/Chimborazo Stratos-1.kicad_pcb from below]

Board: 2 copper layers, 45.0 x 43.8 mm, 21 parts (3 on the bottom side), 18 nets.

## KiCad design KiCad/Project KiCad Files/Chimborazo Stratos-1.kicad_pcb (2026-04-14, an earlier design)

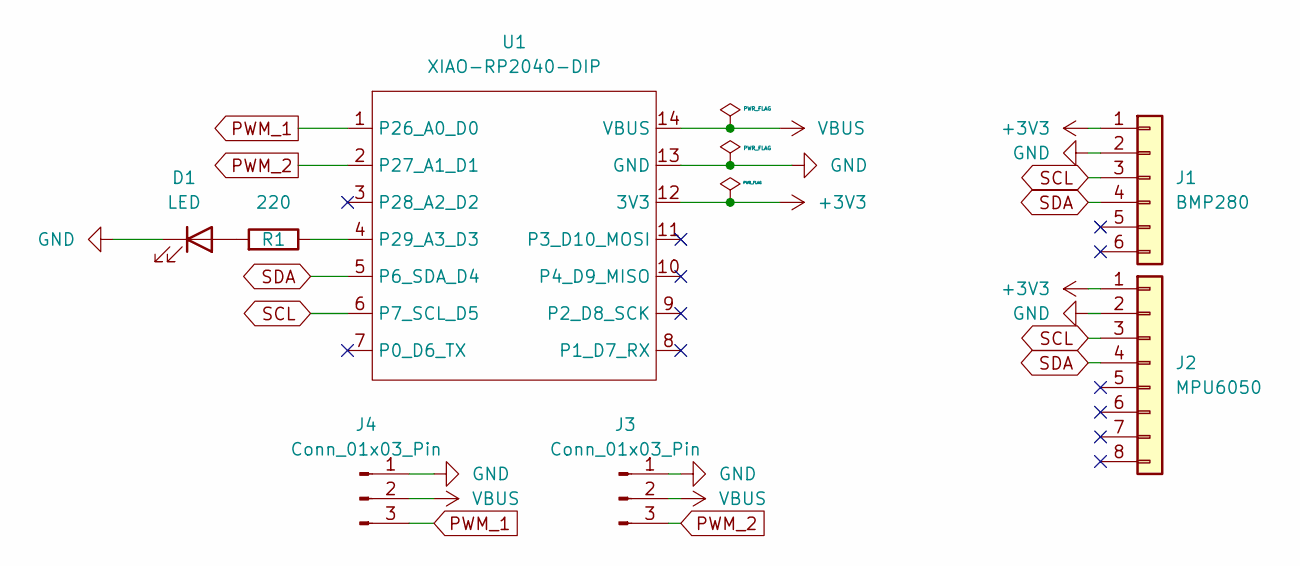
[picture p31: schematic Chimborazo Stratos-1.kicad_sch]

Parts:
D1: LED; LED_D5.0mm
J1: BMP280; PinHeader_1x06_P2.54mm_Vertical
J2: MPU6050; PinHeader_1x08_P2.54mm_Vertical
J3, J4: Conn_01x03_Pin; FanPinHeader_1x03_P2.54mm_Vertical
R1: 220; R_Axial_DIN0207_L6.3mm_D2.5mm_P7.62mm_Horizontal
U1: XIAO-RP2040-DIP

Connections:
+3V3: J1.1, J2.1, U1.12 (3V3)
GND: D1.1 (K), J1.2, J2.2, J3.1, J4.1, U1.13 (GND)
unnamed: D1.2 (A), R1.2
unnamed: R1.1, U1.4 (P29_A3_D3)
PWM_1: J4.3, U1.1 (P26_A0_D0)
PWM_2: J3.3, U1.2 (P27_A1_D1)
SCL: J1.3, J2.3, U1.6 (P7_SCL_D5)
SDA: J1.4, J2.4, U1.5 (P6_SDA_D4)
VBUS: J3.2, J4.2, U1.14 (VBUS)

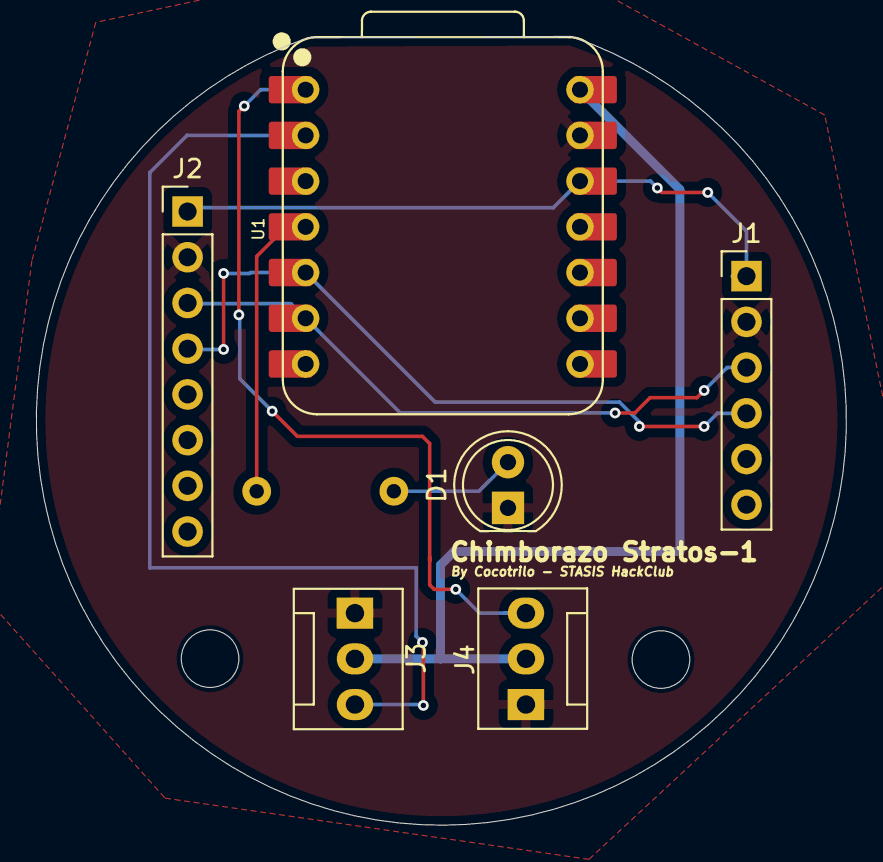
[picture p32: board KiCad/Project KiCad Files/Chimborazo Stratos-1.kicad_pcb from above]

Board: 2 copper layers, 45.0 x 43.8 mm, 7 parts (1 on the bottom side), 9 nets.

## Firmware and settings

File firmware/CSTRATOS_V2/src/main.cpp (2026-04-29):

#include <Arduino.h>
#include <Wire.h>
#include <Adafruit_BMP085.h>
#include <ESP32Servo.h>
#include <MPU6050.h>


// pins
const int PIN_BAT_SENSE = 0;
const int PIN_SERVO1 = 1;
const int PIN_SERVO2 = 2;
const int PIN_PYRO = 21;
const int PIN_SDA = 22;
const int PIN_SCL = 23;
const int PIN_GPS_TX = 16;
const int PIN_GPS_RX = 17;
const int PIN_LED_ARMED = 20;
const int PIN_LED_ERROR = 18;

// altitude and ignition
float max_altitude = 0;
float ground_altitude = 0;
bool recovery_fired = false;


Adafruit_BMP085 bmp;
Servo servo1;
Servo servo2;
MPU6050 mpu;
int16_t ax, ay, az;
int16_t gx, gy, gz;

void setup() {
    Serial.begin(115200);
    pinMode(PIN_LED_ARMED, OUTPUT);
    pinMode(PIN_LED_ERROR, OUTPUT);
    pinMode(PIN_PYRO, OUTPUT);
    digitalWrite(PIN_PYRO, LOW);

    Wire.begin(PIN_SDA, PIN_SCL);
    delay(100);
    // BMP Altitude barometer
    if (!bmp.begin()) {
        digitalWrite(PIN_LED_ERROR, HIGH);
        Serial.println("Error No BMP");
        while (1);
    }

    float sum = 0;
    for(int i=0; i<10; i++) {
        sum += bmp.readAltitude();
        delay(50);
    }
    ground_altitude = sum / 10.0;

    // Accelerometer MPU6050
    Serial.println("Testing MPU");
    mpu.initialize();
    if (!mpu.testConnection()) {
        Serial.println("Error: MPU6050 no MPU");
        digitalWrite(PIN_LED_ERROR, HIGH);
    }
    // servos
    servo1.attach(PIN_SERVO1);
    servo2.attach(PIN_SERVO2);
    servo1.write(90); // 90 degrees
    servo2.write(90);

    // gps
    Serial1.begin(9600, SERIAL_8N1, PIN_GPS_RX, PIN_GPS_TX);

    digitalWrite(PIN_LED_ARMED, HIGH);
    Serial.println("System Ready");


}

void loop() {
    // bat sense
    int raw_bat = analogRead(PIN_BAT_SENSE);
    float voltage = (raw_bat / 4095.0) * 3.3 * 3.0;

    // altitude
    float current_alt = bmp.readAltitude();
    float relative_alt = current_alt - ground_altitude;

    if (relative_alt > max_altitude) {
        max_altitude = relative_alt;
    }

    // MPU
    mpu.getMotion6(&ax, &ay, &az, &gx, &gy, &gz);


    if (!recovery_fired) {
        // El Giroscopio nos da valores entre -32768 y 32767
        // Mapeamos el eje X (gx) para el Servo 1 y el eje Y (gy) para el Servo 2
        int angle1 = map(gx, -15000, 15000, 70, 110);
        int angle2 = map(gy, -15000, 15000, 70, 110);
        
        servo1.write(constrain(angle1, 70, 110));
        servo2.write(constrain(angle2, 70, 110));
    } else {
        // Si el paracaídas ya salió, ponemos los canards en posición neutral (90°)
        servo1.write(90);
        servo2.write(90);
    }

    if (max_altitude > 2.0 && (max_altitude - relative_alt) > 0.5 && !recovery_fired) {
        digitalWrite(PIN_PYRO, HIGH);
        Serial.println("!!DEPLOY!!");

        digitalWrite(PIN_LED_ARMED, LOW);
        digitalWrite(PIN_LED_ERROR, HIGH);

        delay(2000);
        digitalWrite(PIN_PYRO, LOW);
        recovery_fired = true;

    }

    Serial.printf("Alt: %.2f | Max: %.2f | Bat: %.2fV | Gx: %d\n", relative_alt, max_altitude, voltage, gx);
    
    if (voltage < 3.5) {
        digitalWrite(PIN_LED_ERROR, HIGH); 
    } else if (!recovery_fired) {
        digitalWrite(PIN_LED_ERROR, LOW);
    }

    delay(50);
}

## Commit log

2026-04-08 Organizing project structure and adding KiCad libraries and connecting to Github
    [Chimborazo Stratos-1.kicad_pcb, Chimborazo Stratos-1.kicad_sch]
2026-04-08 fixed long path errors and cleaned up libraries, finally I added the libs for the project it was REALLY HARD AND I DONT KNOW WHY :( but I managed to overcome the challenge
    [Chimborazo Stratos-1.kicad_sch, TEST.kicad_pcb, TEST.kicad_sch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]
2026-04-08 Schematic prototype done
    [Chimborazo Stratos-1.kicad_sch]
2026-04-09 PCB model 1 finalized
    [Chimborazo Stratos-1.kicad_pcb, Chimborazo Stratos-1.kicad_sch]
2026-04-09 Final PCB done!
    [Chimborazo Stratos-1.kicad_pcb]
2026-04-13 New PCB OF 45mm Diameter finished :)
    [Chimborazo Stratos-1.kicad_pcb, Chimborazo Stratos-1.step]
2026-04-13 FORGOT TO ADD THE INFIL OF GND SORRYgit add .!
2026-04-14 Re-work of pcb and CAD model
    [1.27mm Right Angle Pinhead 20.step, 100mil Female Pin Header.SLDPRT, 100mil Female Pin Header_2P_Bk.STEP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]
2026-04-14 Finished the pcb and the cad model REAL NO FAKE
    [Chimborazo Stratos-1.kicad_pcb, Chimborazo Stratos-1.kicad_sch, Chimborazo Stratos-1.step]
2026-04-15 Update README with schematic and model images
    Added schematic, PCB, and CAD model images to README.
2026-04-15 Reorganized folders and Added the GERBERS files
    [Chimborazo Stratos-1-B_Cu.gbr, Chimborazo Stratos-1-B_Mask.gbr, Chimborazo Stratos-1-B_Paste.gbr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]
2026-04-15 Final screenshots!
    [Chimborazo Stratos-1.f3d]
2026-04-29 Remade schmeatic changed components and Remade PCB with new and improved layout
    [Chimborazo Stratos-1.kicad_pcb, Chimborazo Stratos-1.kicad_sch]
2026-04-29 Update BOM section with new components and links
2026-04-29 Added BOM firmware, CAD, Schematic update, and more Images
    [1.27mm Right Angle Pinhead 20.step, 100mil Female Pin Header.SLDPRT, 100mil Female Pin Header_2P_Bk.STEP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]
